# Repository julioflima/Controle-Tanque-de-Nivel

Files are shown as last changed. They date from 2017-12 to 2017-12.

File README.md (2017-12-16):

# Controle Tanque de Nível
## Projeto de Controle de Sistemas Dinâmicos - Engenharia Elétrica  - UFC

  Este projeto destina-se ao desenvolvimento de um controle de tanque de nível utilizando os conceitos de malha fechada. Como conrolador e sensor foram escolhidos respectivamente, o ATMEGA168-P e o HC-SR04.

  Os sistemas automáticos de níveis de água atualmente estão presentes em boa parte no cotidiano da vida humana, sejam em industrias ou mesmo nas casas, tendo em vista os conceitos de reutilização ou captação de água. Para controlar estes tipos de sistemas, geralmente utilizam-se de sensores de nível para acionamento da bomba e o controle pode ser feito a partir de um controlador PID ou por histerese, por exemplo. O relatório referente a este projeto se limitará à um controle realizado com base na histerese de sistemas de controle, nos quais os procedimentos serão apresentados mais adiante. A figura abaixo mostra um exemplo esquemático de um sistema hidráulico controlado pela bomba.

<p align="center">
  
</p>

  Para o sistema controlado, a histerese é implementada na forma dinâmica de um determinado atraso da saída em referência com a entrada, desde que esta seja lentamente variável. Este tipo de histerese é uma relação de dependência de taxas, ou seja, pode funcionar com sistemas que necessitem de armazenamento durável de memória. Esta técnica como controlador serve basicamente para filtragem de sinais a fim de que se obtenha uma saída mais lenta de acordo com a memória armazenada de um sinal mais recente. 
Em um sistema baseado em ações liga/desliga, este controle reduz a vida útil ou afeta os dispositivos conectados a este sistema. Por isso, a utilização da técnica de histerese torna-se interessante para sistemas do tipo, resultando, assim, em uma seleção de uma determinada faixa, por exemplo com temperatura, como mostra abaixo.

<p align="center">
  
</p>

  A IHM desenvolvida, teve como intuito a facilidade na hora de interagir na mudança do valor de referência e na visualização do nível atual do tanque independentemente da medição analógica, essa por meio de um duto transparente. Nela foi utilizada um display LCD 16x2, onde é possível a verificação dos valores. Dois botões para mudança no valor da referência. Dois barramentos, um destinado ao sensor ultrassônico, e o outro destinado a placa de driver. Uma saída seria, onde os valores de PWM, nível do tanque e valore de referência, são enviados ao computador para análise. Assim como o micro controlador ATMEGA328-P, responsável pelo controle e aquisição de dados. O esquemático e a placa discorrida nesta seção encontra-se nos anexos do relatório.
  
<p align="center">
  
</p>

  O sensor utilizado neste projeto é o sensor ultrassônico HC-SR04, utilizado para medir distâncias entre 2cm até 4m. Com o intuito de fixação na estrutura desenvolvia, o sensor foi encapsulado em um case como mostra a figura abaixo. O esquemático discorrido nesta seção, assim como mais detalhes encontra-se nos anexos do relatório.

<p align="center">
  
</p>

  O driver representa a parte de potência de um projeto, sendo este responsável pelo chaveamento de uma alta corrente, pois o controlador não suporta esse nível de potência, sendo assim indispensável. A placa de controle desenvolvida segue abaixo na figura abaixo.

<p align="center">
  
</p>

  Segue abaixo os gráficos relativos a dinâmica desse sistema, com o controle desenvolvido até então. Em verde o PWM, em vermelho a referência e em azul a elevação do nível da água.

<p align="center">
  
</p>

## FORK IT!

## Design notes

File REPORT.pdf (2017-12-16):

UFC - Campus Sobral

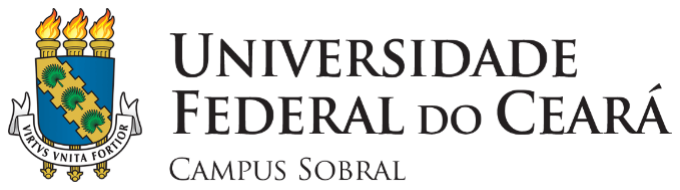
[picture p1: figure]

Controle de Sistemas Dinâmicos Professor Reuber Regis de Melo

Curso de Engenharia Elétrica

Laboratório de Sistemas de Controle

## Controle de Tanque de Nível

Alunos: Denisia Vasconcelos Mota

Julio Cesar Ferreira Lima

Renato Fonteles de Sousa

Prof.: Reuber Regis de Melo

Sobral, Dezembro de 2017

# SUMÁRIO

# INTRODUÇÃO

Os sistemas automáticos de níveis de água atualmente estão presentes em boa parte no cotidiano da vida humana, sejam em industrias ou mesmo nas casas, tendo em vista os conceitos de reutilização ou captação de água. Para controlar estes tipos de sistemas, geralmente utilizam-se de sensores de nível para acionamento da bomba e o controle pode ser feito a partir de um controlador PID ou por histerese, por exemplo. O relatório referente a este projeto se limitará à um controle realizado com base na histerese de sistemas de controle, nos quais os procedimentos serão apresentados mais adiante. A Figura 1.1 mostra um exemplo esquemático de um sistema hidráulico controlado pela bomba.

Figura 1.1 – Sistema hidráulico controlado.

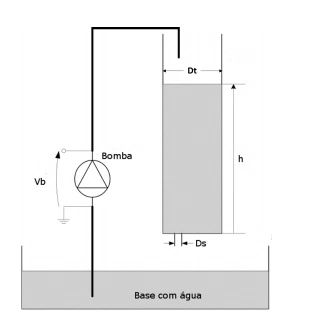
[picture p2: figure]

Fonte: Reuber Regis

Em um sistema deste tipo, é necessário saber alguns parâmetros para se atingir os níveis conforme se deseja no projeto implementado. Um destes parâmetros é o fluxo de entrada de líquido no tanque, que pode ser obtido com a equação (1) a seguir:
Fe = KbVb | (1)

Onde Kb é a constante de fluxo da bomba e Vb a tensão elétrica na mesma
Já a velocidade deste fluxo pode ser dada pela equação de Bernoulli, mostrada na equação (2) a seguir.
vs = √2gℎ | (2)

Onde g é a aceleração da gravidade e ℎ a altura de líquido no tanque.
A área e orifício do tanque podem calculados de acordo com o formato do tanque e do orifício. Para um tanque e orifício com formato cilíndrico, as áreas dos mesmo podem ser calculados conforme as equações (3) e (4) a seguir, respectivamente.

At =

πDt

2
4 | (3)

As =

πDs

2
4

(4)

Pode-se também com as equações já obtidas o fluxo de saída de líquido do tanque multiplicado a área do orifício pela velocidade do fluxo. Para o caso do formato cilíndrico de orifício, com a equação (5) obtém-se o fluxo de saída.
Fs = As√2gℎ | (5)

Assim, a taxa de fluxo do tanque pode ser obtida com a subtração entre o fluxo de entrada e o fluxo de entrada, resultando na equação (6) a seguir.
Ft = KbVb − As√2gℎ | (5)

Pode-se dizer que a taxa de fluxo do tanque é a derivada do volume em relação ao tempo e o volume pode ser calculado como a altura multiplicada pela área do tanque. Logo, de acordo com a equação (5) acima, após substituído o volume por Asℎ na derivada, pode-se isolar o ℎ. Encontra-se, assim, a equação (6) a seguir. dℎ dt =

KbVb − As√2gℎ At | (6)

Integra-se (6) para se encontrar uma equação para a altura. A equação (7) mostra a equação obtida:

ℎ(t) = ∫

KbVb − As√2gℎ
At

(7)

Para o equilíbrio do sistema, é necessário que o mesmo esteja no chamado ponto de operação. Pode-se assim linearizar a (7) a partir dos três primeiros termos da série de Fourier. Seja ℎ̂ = ℎ − ℎ0 e V̂b = Vb − Vb0 para pequenas variações de altura e tensão na bomba e o sistema atuante em um ponto de operação onde a taxa de fluxo seja igual a zero, a equação (8) mostra o resultado da equação linearizada para o projeto.
dℎ
dt = −

Asg√2
2At√gℎ0

ℎ̂ +

KbV̂b
At

(8)

Se na equação acima, for utilizado ℎ̂, como a derivada de ℎ0 é constante, pode-se escrever (8) como: dℎ̂
dt +

Asg√2
2At√gℎ0

=

KbV̂b
At

(8)

Aplicando a transformada de Laplace na equação (8), encontra-se a função transferência do sistema mostrada na equação (9).

G(s) =

Ĥ(s)
V̂b(s)

=

2Kb√gℎ0
2√gℎ0sAt + As√2g

(9)

Onde, da equação (9), pode-se generalizara função normalizada de malha aberta como na equação (10) a seguir.
G(s) =

Kdc
τs + 1

(10)

Onde Kdc (ganho DC) e τ (constante de tempo) são conforme (11) e (12), respectivamente:

Kdc =

Kb√gℎ0√2
Asg

(11)

τ =

√gℎ0sAt√2
Asg

(12)

Para o sistema controlado, a histerese é implementada na forma dinâmica de um determinado atraso da saída em referência com a entrada, desde que esta seja lentamente variável. Este tipo de histerese é uma relação de dependência de taxas, ou seja, pode funcionar com sistemas que necessitem de armazenamento durável de memória. Esta técnica como controlador serve basicamente para filtragem de sinais a fim de que se obtenha uma saída mais lenta de acordo com a memória armazenada de um sinal mais recente.
Em um sistema baseado em ações liga/desliga, este controle reduz a vida útil ou afeta os dispositivos conectados a este sistema. Por isso, a utilização da técnica de histerese torna-se interessante para sistemas do tipo, resultando, assim, em uma seleção de uma determinada faixa, por exemplo com temperatura, como mostra Figura 1.2.

Figura 1.2 – Exemplo de Histerese para temperatura.

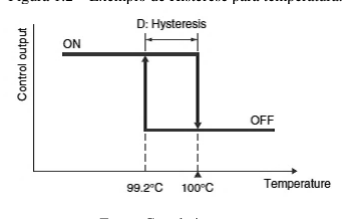
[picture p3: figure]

Fonte: Google imagens,

Onde na figura 02, duty cycle igual a 0,8 ºC para o valor de histerese 0,2%, a saída do sistema é desligada em 100 ºC e novamente ligada caso atinja a temperatura de 99.2 ºC.

# DESENVOLVIMENTO

## 1. Tanque

Para a construção do sistema físico foi feito uso de tubulações em PVC a fim de se obter caminho e encanamento para o fluxo de água, como também base e estrutura do mesmo material para o próprio sistema. Além disso, fez-se necessária na montagem a aplicação da bomba d’água do sistema ao lado inferior do tanque de reservatório, com intuito de garantir sempre a realimentação de água dentro das engrenagens da bomba. O resultado do sistema é mostrado abaixo pela Figura 2.1.

Figura 2.1 e 2.2 – (b) Sistema físico; (a) Posição da bomba d’água.

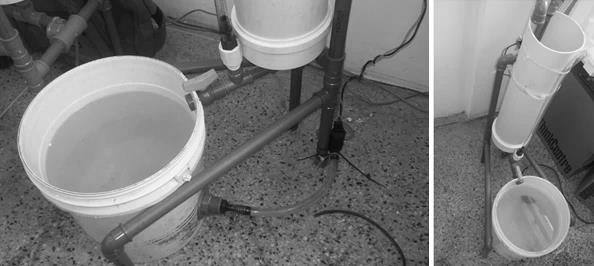
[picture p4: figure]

(a) (b)
Fonte: Próprio autor.

Como ilustra a Figura 2.2, para o tanque com altura a ser controlada, a equipe o construiu no sistema com tubulação de 150mm de diâmetro, uma altura máxima de 80 cm. O Reservatório trata-se de um balde com capacidade até 25 Litros, e para tubulação de fluxo e a estrutura de sustentação de 4 apoios, a matéria prima foi materiais de encanamento de 20 e 25 mm respectivamente de diâmetro. Assim, para o equacionamento, o tanque terá uma área de 56,25 cm².
Da equação 01, para o sistema utilizado em questão faz-se necessário saber as características físicas da bomba d’água utilizada. O grupo optou por utilizar um motor de corrente contínua utilizado em para-brisas de automóveis, com sua alimentação sendo 12V e máximos de corrente de aproximadamente 4,5 A. A Figura 2.3 a seguir mostra o modelo da bomba utilizada na implementação do projeto

Figura 2.3 – Bomba d’água TSN 12V.

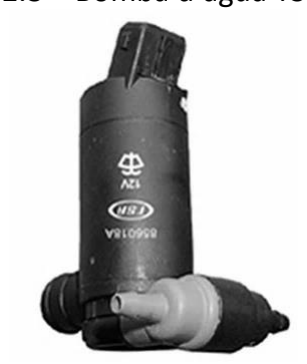
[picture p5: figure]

Fonte: Google Imagens.

Com isso, para o sistema utilizado, foi decidido utilizar como sinal de comando para a bomba um sinal PWM (Pulse Width Modulation) que se trata de um sinal periódico com ciclo de trabalho “d” variável, pois neste caminho, garantia-se valores de tensão os quais a bomba foi projetada, sempre em 0 ou 12 volts, diminuindo erros e não linearidades providas pela bomba. Dessa forma, a equação 01 terá uma relação periódica, onde deve ser utilizado a tensão média, calculada por:

Fe = Kb × Vbmédio

(13)

Ou seja, o cálculo dos valores médios de tensão na bomba Vbmédio dar-se pela seguinte forma:

Vbmédio =

1
T

∫ Vb

(t) × dt = ∫ 12 × dt

T∗d

0

T

0

+ ∫ 0 × dt

T

T∗d

= 12 × d | (14)

Portanto, substituindo a equação acima em 13, temos:

Fe = Kb × (d × 12)

(15)

Logo, para encontrar a constante da bomba, faz-se necessária o uso também de sinal PWM, o qual terá relação entre o fluxo dado pela equação anterior.

Com isso, de forma empírica, a equipe obteve no experimento medições de variação de altura da coluna d’água do sistema e qual o tempo levou esta variação de volume para determinado valor de ciclo de trabalho (d). Com a utilização de um micro controlador, junto a um circuito de chaveamento com MOSFET IRFZ648N, para experimento com a finalidade de se obter a constante da bomba, foi montado um circuito driver para a bomba d´água de acordo com o esquemático da Figura 2.5 a seguir:
Em seguida, com um programa simples dentro do micro controlador, de forma a guardar uma variável do tipo float em linguagem C/C++, o código simples é apenas um chaveamento com sinal alto no instante de tempo do ciclo de trabalho, e o desligamento no resto do período. Dessa forma, variando o valor da variável de ciclo de trabalho d, tem-se os resultados obtidos das medições feitas na tabela abaixo:

Tabela 2.1 – Variáveis para cálculo da constante da bomba Kb.
Ciclo de Trabalho | Δ Altura(m) | Δ Tempo(s) | Δ Volume(cm³) | Fluxo (cm³/s) | Kb
0,60 | 0,10 | 41,96 | 1767,14550 | 42,1150024 | 5,8493
0,70 | 0,10 | 58,27 | 1767,14550 | 30,3268492 | 3,6103
0,75 | 0,20 | 68,57 | 3534,29100 | 51,5428176 | 5,7270
0,80 | 0,06 | 19,61 | 1060,28730 | 54,0687047 | 5,6322
0,85 | 0,20 | 65,46 | 3534,29100 | 53,9916132 | 5,2933
0,90 | 0,10 | 31,90 | 1767,14550 | 55,3964107 | 5,1293
1,00 | 0,10 | 27,58 | 1767,14550 | 64,0734409 | 5,3395

Para os cálculos da tabela, com um cronômetro foi medido no sistema a variação da altura e qual o tempo em que o sistema levou para atingir àquela altura. Como os valores de área do cilindro de 75mm de raio são conhecidos, a variação do volume pode ser obtida. Por fim, o cálculo do fluxo é simplesmente a razão entre a variação do volume com a variação do tempo, onde com a equação 15, foi feita a coluna da tabela 01 para cálculo de Kb com a seguinte equação:

Kb(d) =

Fb
d × 12 =

∆Volume
∆tempo
d × 12

16

Fazendo um gráfico de dispersão, é possível notar os diferentes modos de comportamento da bomba, como mostra a Figura 2.4;

Figura 2.4 - Gráfico de dispersão para eixo x ciclo de trabalho e eixo y constante Kb.

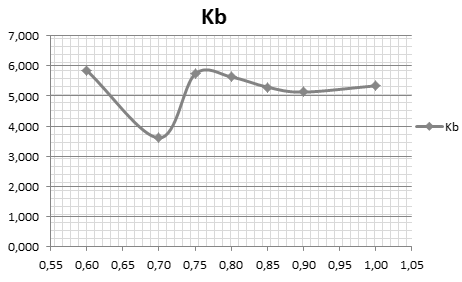
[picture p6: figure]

Fonte: Próprio autor.

Do gráfico, é notório a o erro relacionada a medição em “d” igual a 0,7, o que define um erro no momento da medição por fatores de problemas com a bomba, limitação de corrente da fonte ou a atuação da sobre carga que neste caso teve efeito maior por mudanças físicas da quantidade de água na bomba. Com isso, é válido fazer o cálculo final na constante Kb ignorando esses tipos de extremos encontrados.
Então, para o cálculo da constante Kb, pode-se adotar um dos valores encontrados, ou fazer um levantamento em cima das diferentes medições, calculando uma média aritmética da constante, que resultará em:

Kb =

5,849 + 5,727 + 5,632 + 5,293 + 5,129 + 5,329 6

= 5,945 | 17

Ainda no sistema físico, a equipe utilizou de uma chave reguladora de fluxo a fim de se ter controle quanto a vazão do fluxo de saída, permitindo assim ajustá-lo de acordo com a dinâmica do resto do sistema. Contudo, para o equacionamento faz-se necessária a área da secção transversal onde o fluxo cai no reservatório, algo quase impossível de se obter com equipamentos de medições ao tentar medir na chave reguladora de fluxo. Partindo da equação 5, sabemos que a área será:

As =

Fs
√2 × g × ℎ

=

1
√2 × g × ℎ

×

∆volume
∆tempo | 16

Então, a equação acima mostra que, com um valor constante de uma coluna d’água, calculando uma variação de volume e o tempo gasto, é possível estimar a área da secção transversal da vazão. Dessa forma, o grupo fez de forma empírica um experimento com intuito de calcular a área AD, mantendo uma altura h de 40cm. Com gravidade sendo 982 cm/s², temos a tabela feita para 5 medições da área, e uma estimativa média sendo: Tabela 2.2 – Estimativa da área da secção transversal do fluxo de saída:
Tempo(s) | Δ Volume (cm³) | Fluxo (cm³/s) | Área (cm²)
17,03 | 500,00 | 29,3599530 | 0,1048
16,21 | 490,00 | 30,2282542 | 0,1078
15,86 | 470,00 | 29,6343001 | 0,1057
15,80 | 450,00 | 28,4810127 | 0,1016
18,13 | 538,96 | 29,7275234 | 0,1061
Área Média | | | 0,1052

Portanto, os experimentos mostraram que o sistema tem constante da bomba KB igual a 5,945 e a área da secção transversal da tubulação de saída foi de 10,52 mm².

## 2. IHM (Interface Homem Máquina)

A IHM desenvolvida, teve como intuito a facilidade na hora de interagir na mudança do valor de referência e na visualização do nível atual do tanque independentemente da medição analógica, essa por meio de um duto transparente. Nela foi utilizada um display LCD 16x2, onde é possível a verificação dos valores. Dois botões para mudança no valor da referência. Dois barramentos, um destinado ao sensor ultrassônico, e o outro destinado a placa de driver. Uma saída seria, onde os valores de PWM, nível do tanque e valore de referência, são enviados ao computador para análise. Assim como o micro controlador ATMEGA168-P, responsável pelo controle e aquisição de dados. O esquemático e a placa discorrida nesta seção encontra-se nos anexos deste relatório.

Figura 2.5 – Placa desenvolvida para IHM.

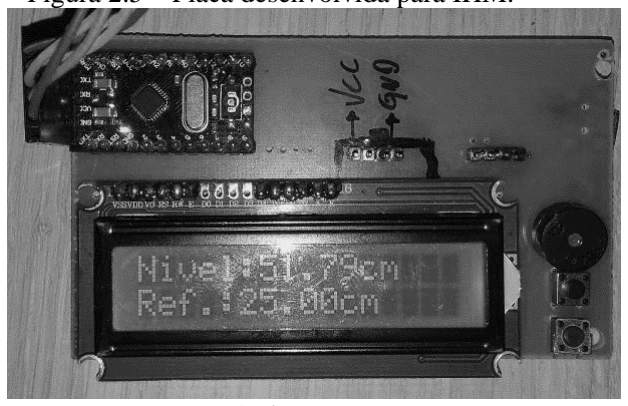
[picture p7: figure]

Fonte: Próprio autor.

Além da placa desenvolvida para a IHM, ainda há a possibilidade de conexão a um computador e assim fazer a análise dos dados. No entanto esse não é a principal vantagem desta conexão com a serial, e sim a possível plotagem dos gráficos e análise da dinâmica do sistema. Este é um dos grandes diferenciais deste projeto.

## 3. Sensor

O sensor utilizado neste projeto é o sensor ultrassônico HC-SR04, utilizado para medir distâncias entre 2cm até 4m. Com o intuito de fixação na estrutura desenvolvia, o sensor foi encapsulado em um case como mostra a Figura 2.6 abaixo.

Figura 2.6 – Sensor ultrassônico envolto em um case.

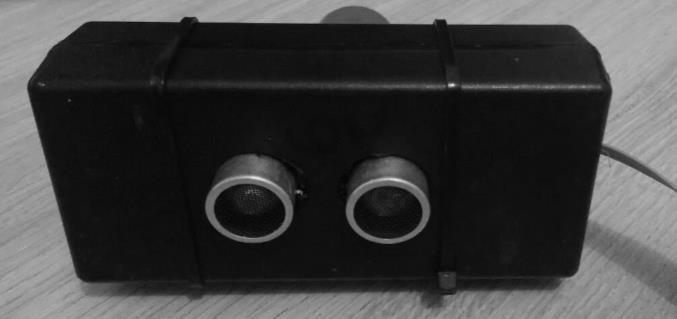
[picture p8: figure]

Fonte: Próprio autor.

O princípio de funcionamento deste sensor é baseado na velocidade do som no ar que é constate e de valor igual a 346,3m/s² se medido a CNTP. Por se tratar de uma grandeza constante, quando o sensor envia um pulso de sinal sonoro ele se propagará na velocidade do som, percorrerá o caminho, baterá no sólido, se encontrar um, a uma distância de até 4m e retornará o ECHO. Assim o micro controlador após o envio do sinal dispara um contador que só irá parar quando o ECHO for retornado, o valor deste contador multiplicado pela constante de velocidade do som no ar irá proporcionar o valor da distância percorrida, que deverá ser dividida por dois, pois esta representa a distância de ida e retorno do sinal de som, pois como o caminho percorrido é o mesmo, ambas são iguais. A Figura 2.7 abaixo ilustra o processo elencado acima. Já a Figura 2.8 ilustra o processo da variação do sinal elétrico que acontece nas portas digitais do micro controlador.

Figura 2.7 – Processo de medição de distância com sensor ultrassônico.

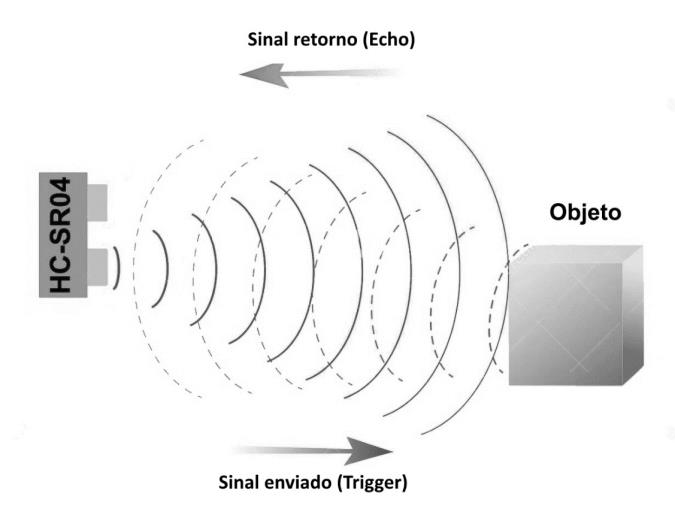
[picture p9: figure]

Fonte: Blog FilipeFlop.

Figura 2.8 – Processo elétrico nas I/Os do micro controlador.

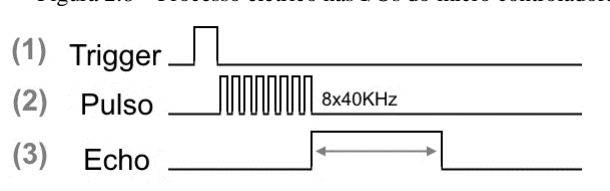
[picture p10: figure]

Fonte: Blog FilipeFlop.

## 4. Driver

O driver representa a parte de potência de um projeto, sendo este responsável pelo chaveamento de uma alta corrente, pois o controlador não suporta esse nível de potência, sendo assim indispensável. A placa de controle desenvolvida segue abaixo na Figura 2.9.

Figura 2.9 – Placa de circuito do driver.

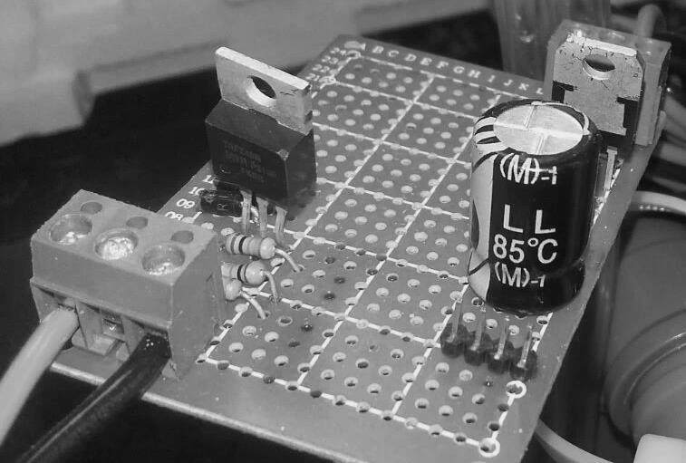
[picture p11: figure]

Fonte: Próprio autor.

A placa consiste em um borne para alimentação em 12V CC, e outro para a conexão com a bomba d’água, motor CC, neste caso. O pino de 12V parte direto para um dos terminais do motor, e a saída do motor será conectado no dreno de um MOSFET. Em antiparalelo com o motor será ligado um diodo ultra fast, na função de diodo de roda livre, para que possa fechar a malha e dissipar a corrente armazenada nos enrolamentos do motor, no momento em que ele for desligado, evitando o centelhamento, a propagação de ruído e possíveis problemas relacionados a chaves eletrônicas. Foi escolhido um diodo ultra fast, por conta do seu tempo de recuperação ser elevado, logo ele atuará de maneira rápida conduzindo a corrente, assim que o motor for desligado, ou passar por um ciclo onde a chave eletrônica o desliga. O MOSFET foi escolhido, por conta da sua baixíssima resistência de dreno source e comportando-se quase como uma chave perfeita e evitando, o aquecimento deste, evitando a necessidade de colocação de um dissipador de calor. Na gate do MOSFET foi colocado um resistor de pull-down, assim evita que na presença de um ruído esterno ou instabilidade do sistema o MOSFET conduza. Novamente entre o gate e o borne de conexão com o micro controlador foi colocado um resistor para limitação da corrente oriunda do micro controlador, este resistor não é necessariamente necessário, é apenas uma questão de proteção para o micro controlador em caso de mal funcionamento da chave. O circuito foi pensado de modo a funcionar de maneira desacoplada de duas fontes de alimentação, bastando assim apenas a alimentação da placa do driver. Neste intuito foi inserido um CI de regulação de tensão LM7805, que tem a função de reduzir e mantar na saída 5V CC, com valores de entrada que podem variar de 35V a 5V. Além do regulador foram adicionados uns capacitores para filtragem de frequências altas, assim como controle do ripple oriundo da fonte. A saída deste regulador, juntamente com o ground e pino de entrada para o resistor do gate, foram ligados em um barramento de com 4 pinos, poderiam ser utilizados apenas 3 pinos, porém por uma preferência em manter o padrão oriundo do circuito de IHM, foi optado por manter os quatro e deixando assim um pino não conectado a nada. O esquemático discorrido nesta seção encontra-se nos anexos deste relatório.

## 5. Controle

O controle utilizado neste projeto, foi o PWM (Pulse Width Modutation), que compreende na variação da largura de pulso de uma onda quadrada de frequência fixa, desse modo é variada a energia na saída. No sistema de um motor CC de rotação relativamente baixa o controle com variação de energia, por PWM, em uma frequência de 500Hz é funciona relativamente bem, pois trata-se de uma relação de frequência de controle e frequência de atuação alto, isto é a frequência do controle é muito mais alta que a frequência que o motor trabalha. A variação da energia, ocorre com a variação do duty cicle, que compreende na porcentagem em que o pulso permanece em nível alto, a cada ciclo. Assim a variação do duty cicle provocará a variação da energia variando a tensão média aplicada nos terminais do motor.

Figura 2.10 – Variação de tensão média por PWM.

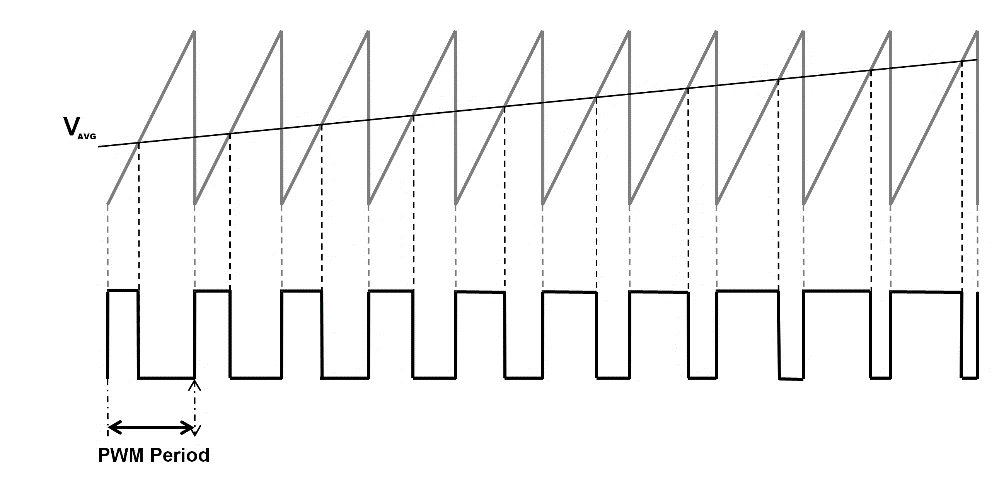
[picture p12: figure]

Fonte: Google imagens, editado pelo autor.

### 1. Definição de Constantes

Primeiramente foram definidas as constantes relativas aos erros provocados pelo tanque nível em relação ao sensor. Após a fixação do sensor em seu devido local de operação, com o tanque vazio foi anotado o valor mostrado. Este valor corresponde a distância total do sensor ao fundo do nível.
Após o processo citado no próximo tópico ainda se observou um erro relativo ao fundo real do tanque em relação a régua de medição, pois o nível indicava um número inferior ao mostrado pelo nível analógico, isso se dá pelas relações não lineares, por conta de conexões da estrutura no fundo do tanque. A diferença que faltava para a que as duas medidas fossem iguais foi anotada.
A constante de histerese trata-se da distância em que o controlador irá preocupar-se com o controle, isto dentro da região de histerese o sistema estabiliza-se, não havendo mais incrementos ou decrementos pelo controlador. Então esta constante precisará ser definida de modo que o sistema não fique demasiado lento, como também não apresente muito ruído ao estabilizar-se. Esta constante foi obtida determinando inicialmente um valor que se acreditava ser um bom parâmetro, de forma intuitiva. A posteriori tal constante foi modificado, para observação se melhores resultados eram encontrados. Ao fim se percebeu que a determinação da constante ideal era a considerada inicialmente.
Precisa-se de um valor inicial para o valor de referência, como o tanque possui cerca de 50cm de comprimento, optou-se pelo valor médio.
Deste modo tais constantes elaboradas seguem abaixo, respectivamente na ordem que foram apresentadas:
- clvlwater: 47.59
- deltaSystem: 0.5
- waterlvl: 25
- offset_lvlwater: 4.2

### 2. Medição

A cada ciclo no main() do programa que acontece a cada 10ms, o micro controlador faz a leitura da distância. No entanto, como neste trabalho o intuito não é a medição da distância do sensor ao nível do tanque e sim do nível zero do tanque até o seu valor mais alto, se subtrai da variável clvlwater o valor de distância medido e por sua vez se soma o erro relativo a medição da distância pelo sensor até o fundo do tanque offset_lvlwater. Dessa forma o sinal resultante é de fato a leitura do nível do tanque em relação ao nível zero.

### 3. Atuação

A atuação, acontecerá de maneira incremental, se a distância capturada estiver acima do nível de referência, será subtraído o duty cicle do PWM e verificado de novo se atendeu a referência, fechando assim a malha para o primeiro caso. O segundo caso é análogo ao primeiro, onde ele irá incrementar o duty cicle do PWM, e então verificar sua distância do ponto de referência. O circuito estabilizará se o nível estiver sempre no nível de referência com uma variação compreendida dentro do intervalo de histerese, ou situado em algum dos limites do duty cicle do PWM, onde não fosse possível o incremento ou o decremento deste, por conta do sistema ser não linear e haver os limites 100% e 0%. Segue na Figura 2.11 abaixo o gráfico gerado em tempo real de acordo com os dados enviados pela porta serial do micro controlador. Em verde o PWM, em vermelho a referência e em azul a elevação do nível da água.

Figura 2.11 – Gráfico da dinâmica do sistema controlado em operação.

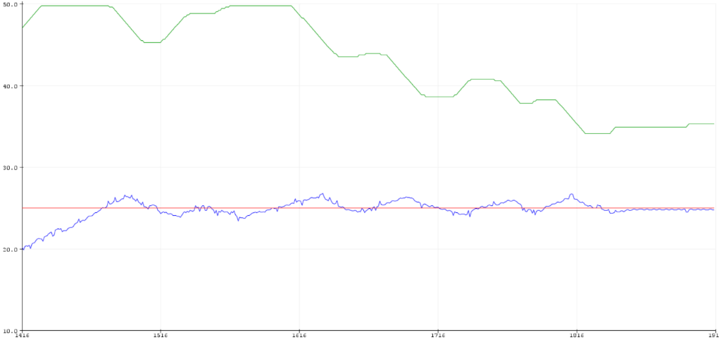
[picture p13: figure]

Fonte: Google imagens, editado pelo autor.

# REPOSITÓRIO PÚBLICO

Este trabalho não tem o intuito de ser descontinuado ao fim desta disciplina, de modo que ele seja

perpetuado e possa contribuir para a formação dos integrantes, juntamente com a formação de alguém que

deseja um fim próximo ao que se destinou aqui. Será postado em uma plataforma aberta, tanto os modelos de

esquemático da placa que envolve o micro controlador e o sensor ultrassônico, quanto a placa de driver de

potência.

Será adicionada uma licença pública de livre modificação e uso de tudo desenvolvido dentro deste

projeto, chamada licença MIT.

O link para acesso do repositório, segue abaixo:

- https://github.com/juloko/Controle-Tanque-de-Nivel

A seções dentro do repositório são divididas abaixo:

- code: Diretório destinado a colocação do código rodado dentro do micro controlador. O ambiente

de desenvolvimento utilizado foi a IDE Arduino.

- libraries: Diretório destinado a colocação das bibliotecas utilizadas dentro do código do micro

controlador. As bibliotecas foram produzidas para a linguagem C, compatível com o compilador

Arduino.

- sensor: Diretório destinado a colocação das do esquemático e placa do sensor, concebido aqui

como a união do circuito do micro controlador com o barramento do sensor. Tais arquivos são

destinados a produção da placa de circuito impresso. Os arquivos encontram-se no formado do

software KICAD.

- driver: Diretório destinado a colocação das do esquemático do circuito de acionamento da bomba,

conhecido como driver, destinada a produção do circuito. Os arquivos encontram-se no formado

do software KICAD.

- REPORT: Arquivo com este relatório.
- README: Arquivo com explanação sobre aspectos gerais deste relatório.

# CONCLUSÃO

Idealmente o controle elaborado nesse projeto, não deveria ter procedido da maneira que foi. O conjunto

micro controlador e sensor, deveria apenas ter funcionado unicamente como um sensor. No entanto a

problemática de não haver um conversor digital analógico, D/A, impossibilitou o prosseguimento do projeto

sem que houvesse a implementação do controlador via código, já que não se conseguiria uma razão de

proporção na entrada do amplificador operacional que fosse possível a comparação de erro.

No entanto, o projeto mostrou-se satisfatório, uma vez que ele consegue atingir o estado permanente. No

entanto não foi possível a estabilização da bomba, pois a resposta do controlador é demasiado lenta em relação

a dinâmica do sistema. Nos gráficos gerados no experimento, foi possível a verificação senoidal na variação

do erro de estado permanente, em torno da referência de nível. Também foi notada uma semelhante relação em

relação ao acionamento da bomba, uma vez que em determinado período de tempo, constante dado pela

constante de tempo característica do sistema, ela comportava-se de maneira senoidal variando entre os limiares

onde havia cem por centro do duty cicle do micro controlador e zero por cento.

# BIBLIOGRAFIA

[1] OGATA, Katsuhiko. Engenharia de Controle Moderno. 4ª edição. Editora Prentice Hall.
[2] REGIS DE MELO, Reuber. Modelagem da dinâmica física do tanque de nível. Laboratório de Controle

de Sistemas Dinâmicos.

[3] POULSEN, Soren. ANDERSEN, Michael A. E. . Hysteresis Controller with constant switching

frequency. Technical University of Denmark. Disponível em:

<http://www.skory.gylcomp.hu/alkatresz/pwm_amp(fixfreq_onrezgo).pdf>. Acesso em Dezembro de

2017.

[4] WIKIPEDIA. Hysteresis. Disponível em: <https://en.wikipedia.org/wiki/Hysteresis>. Acesso em

Dezembro de 2017.

[5] OMRON. Temperature Controller: Hysteresis. Disponível em: <http://www.omron-

ap.com/service_support/FAQ/FAQ00549/index.asp>. Acesso em Dezembro de 2017.

# ANEXOS

// Carrega as bibliotecas, sensor ultrassonico e LCD. #include <Ultrasonic.h>
#include <LiquidCrystal.h>

// Declara a variável de referência do nível da água. float waterLvl = 25;

// Declara a variável que armazena a distância recebida. float distance = 0;

// Declara a variável de tempo para plotar os valores. float timerPrint = 0;

// Declara a variável do duty cicle do PWM.
float duty = 0;

// Declara a variável de tempo para o controlador. float timerControl = 0;

// Define as constantes do sistema.
#define timeSystem 10

#define timeControl 2*timeSystem #define timePrint 100*timeSystem #define clvlwater 47.59

#define offset_lvlwater 4.2

// Define a constantes histerese de distância. #define deltaSystem 0.50

// Declara e define os pinos utilizados pelo LCD.
// Inicializa a biblioteca do LCD, com os pinos que serão utilizados. const int constraste = 10, rs = 4, en = 5, d4 = 6, d5 = 7, d6 = 8, d7 = 9; LiquidCrystal lcd(rs, en, d4, d5, d6, d7);

// Declara e define os pinos para o trigger e echo.
#define pino_trigger 15

#define pino_echo 14

// Inicializa o sensor nos pinos definidos acima. Ultrasonic ultrasonic(pino_trigger, pino_echo);

// Declara e define o pino utilizado no PWM. #define pwm 11

// Define os pinos utilizados nos botões. #define btn_01 2
#define btn_02 3

void setup()
{
// Attach the Extern Interruptions. attachInterrupt(digitalPinToInterrupt(btn_01), upLvl, FALLING); attachInterrupt(digitalPinToInterrupt(btn_02), downLvl, FALLING);

// Muda o constraste do LCD.
analogWrite(constraste, 50);

// Iniciliza a Serial, com sua velocidade.. Serial.begin(9600);

// Seta os números o número linhas e colunas do LCD.

lcd.begin(16, 2);

// Escreva no LCD, Controle Analógico em inglês. ;) lcd.write("Analogic Control");

//Aplica delay de 1s.
delay(2000);
}

void loop()
{
// Recebe distância do nível da água.
distance = getDistance();

// Plota o nível referência do nível da água no LCD, a cada 1s. printLCD(distance);

// Plota o nível referência do nível da água na Serial. printSerial(distance);

// Controla.
pwmDistance((12 / 6) * 255); }

// Exibe informações no LCD, a cada 1s.
void printLCD(float distance) {
if ((millis() - timerPrint) >= timePrint) { timerPrint = millis();

lcd.clear();
lcd.setCursor(0, 0);
lcd.write("Nivel:");
lcd.print(distance);
lcd.print("cm");
lcd.setCursor(0, 1);
lcd.write("Ref.:");
lcd.print(waterLvl);
lcd.print("cm");
}
}

// Exibe informações na Serial.
void printSerial(float distance) { Serial.print("Nivel em cm: "); Serial.print(distance);
Serial.print(" | ");
Serial.print("Referencia em cm: "); Serial.print(waterLvl);
Serial.print(" | ");
Serial.print("Duty: ");
Serial.println((duty / 255) * 50);
}

// Plota no duty do PWM o valor do nível da água. void pwmDistance(float duty) { analogWrite(pwm, duty);
}

// Retorna a distancia do nivel da água. float getDistance() {
float cmMsec;
for (int i = 0; i<1; i++) {
// Lê as informacoes do sensor, em cm.

long microsec = ultrasonic.timing();
cmMsec += ultrasonic.convert(microsec, Ultrasonic::CM); delay(timeSystem);
}
return clvlwater - cmMsec / 1 + offset_lvlwater;
}

// Incrementa em 0.01 o nível de referência da água. void upLvl() {
while (!digitalRead(btn_01)) {
if (waterLvl<50) {
waterLvl += 0.01;
printLCD(distance);
delay(100);
}
}
}

// Decrementa em 0.01 o nível de referência da água. void downLvl() {
while (!digitalRead(btn_02)) {
if (waterLvl>0) {
waterLvl -= 0.01;
printLCD(distance);
delay(100);
}
}
}

void digitalControl(float distance, float waterLvl) {
// Controle de Histerese de Tempo.
// Apenas irá controlar quando o tempo de captura espaçar 200ms desde a última leitura if ((millis() - timerControl) >= timeControl) {
timerControl = millis();

// Controle de Histerese de Distâncias.
// Verifica se a diferença entre o nível e a referência é superiores a 0.5cm. if ((distance - waterLvl) > deltaSystem) {
pwmDistance(setDuty(duty - 1));
}
else if ((distance - waterLvl) < -deltaSystem) { pwmDistance(setDuty(duty + 1));
}
}
}

int setDuty(int _duty) {
if (_duty < 255 && _duty > 0) { duty = _duty;
}
return duty;
}

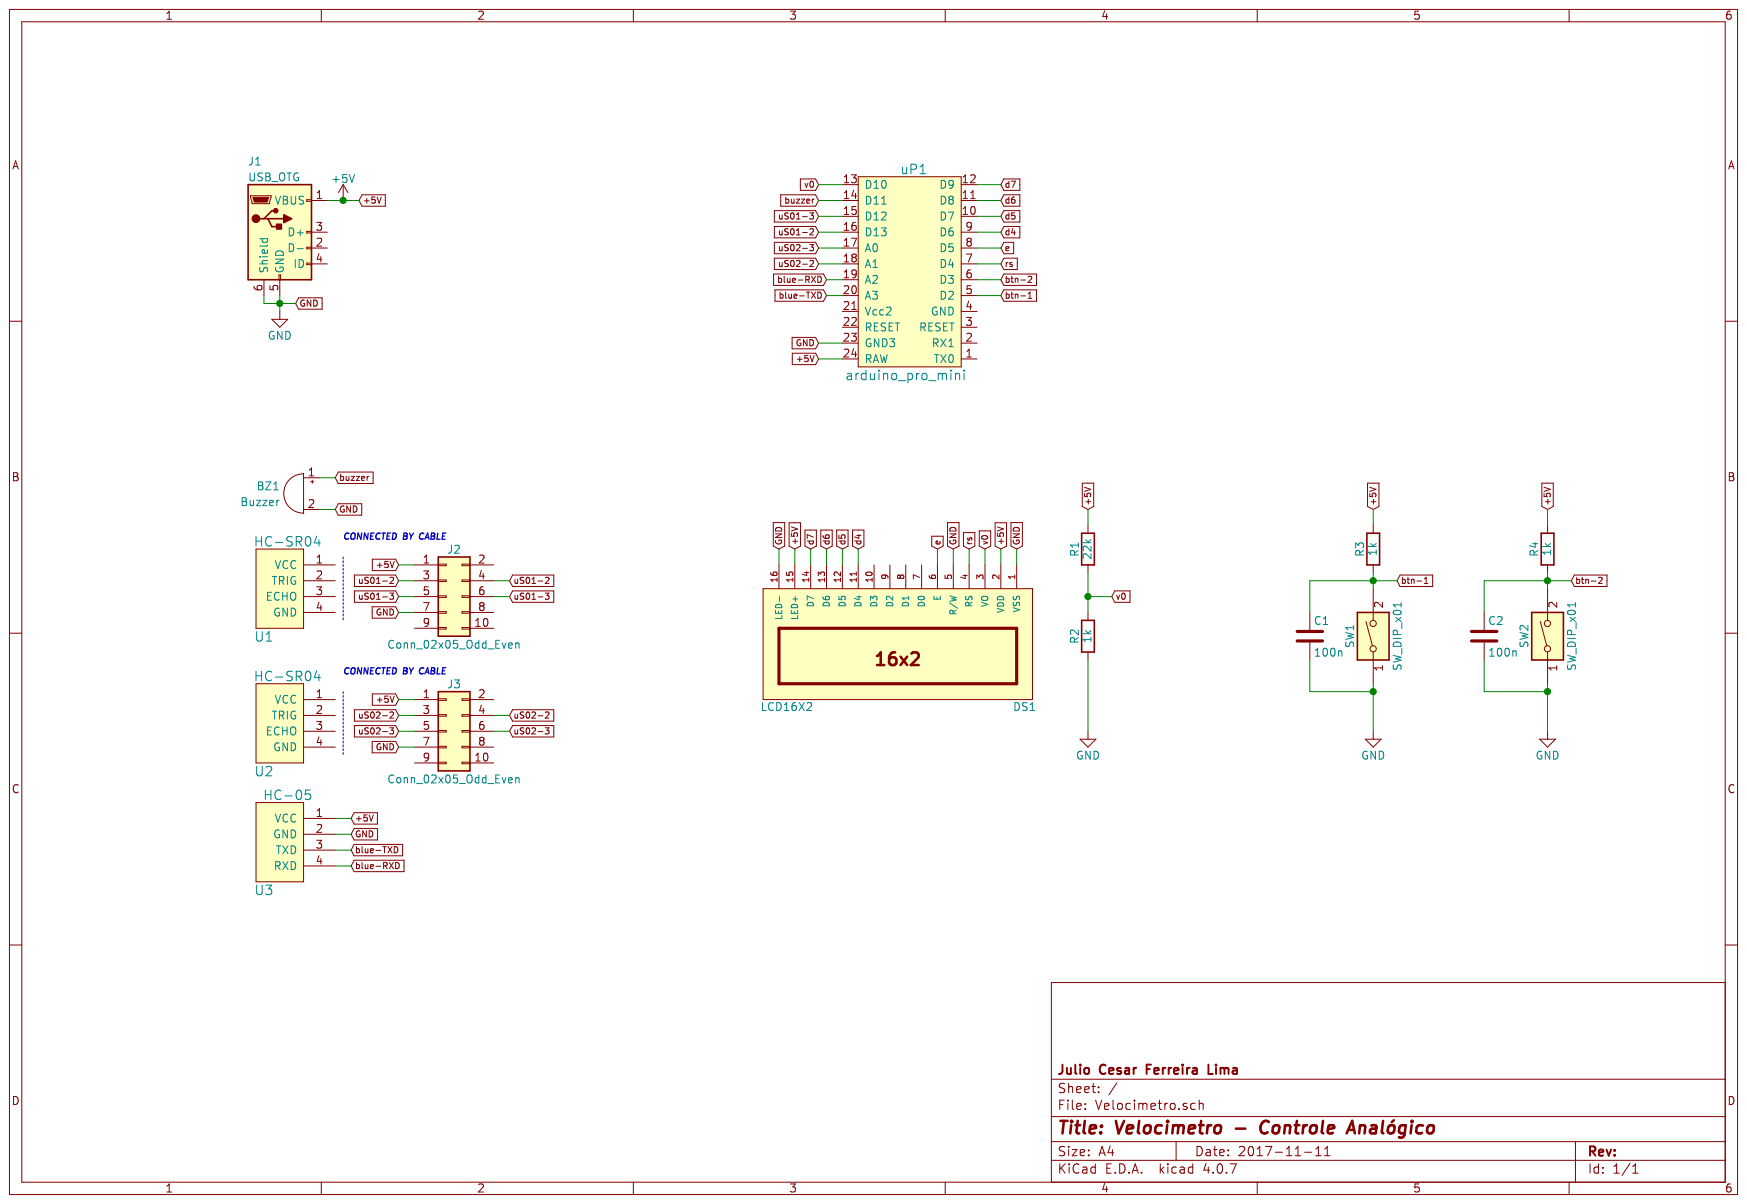
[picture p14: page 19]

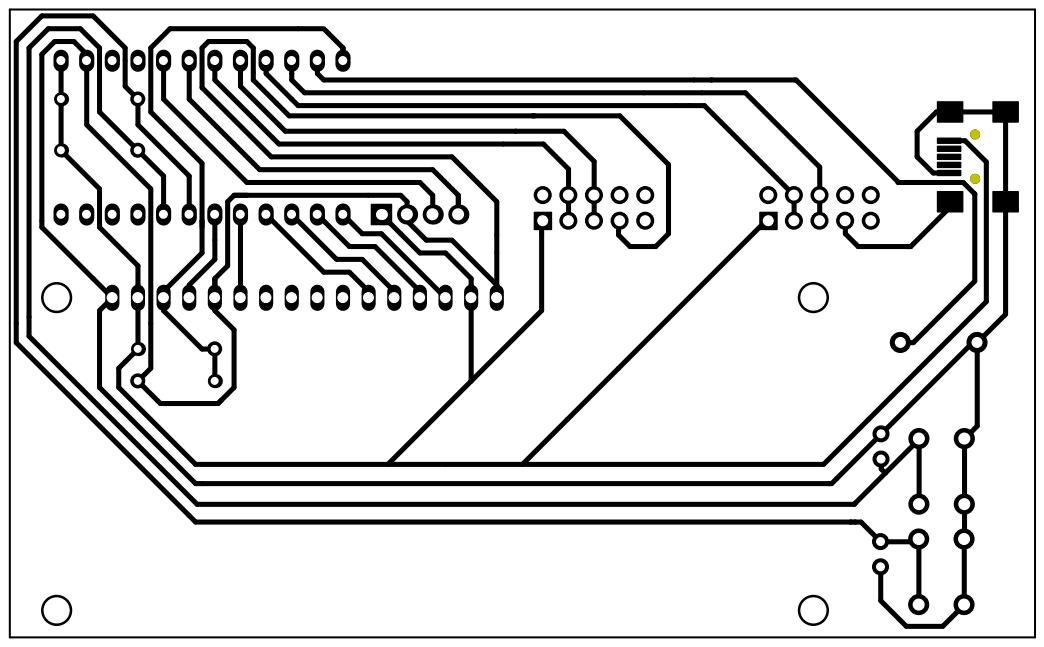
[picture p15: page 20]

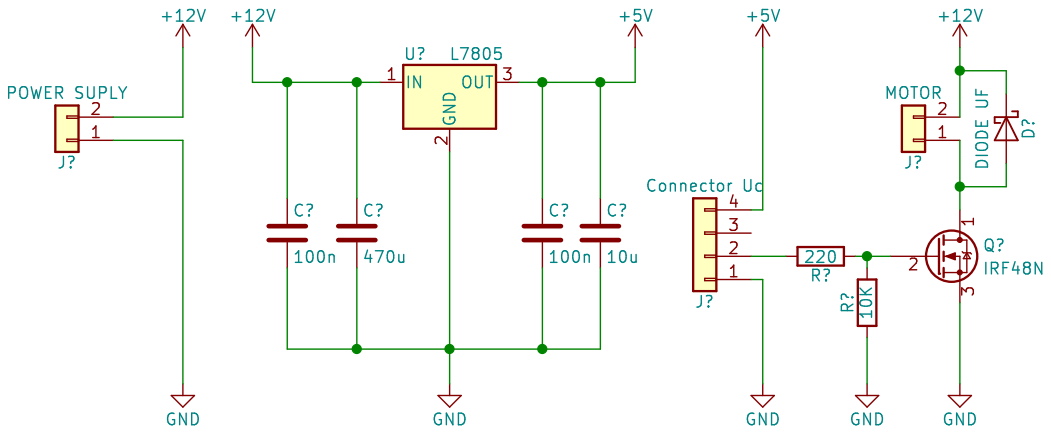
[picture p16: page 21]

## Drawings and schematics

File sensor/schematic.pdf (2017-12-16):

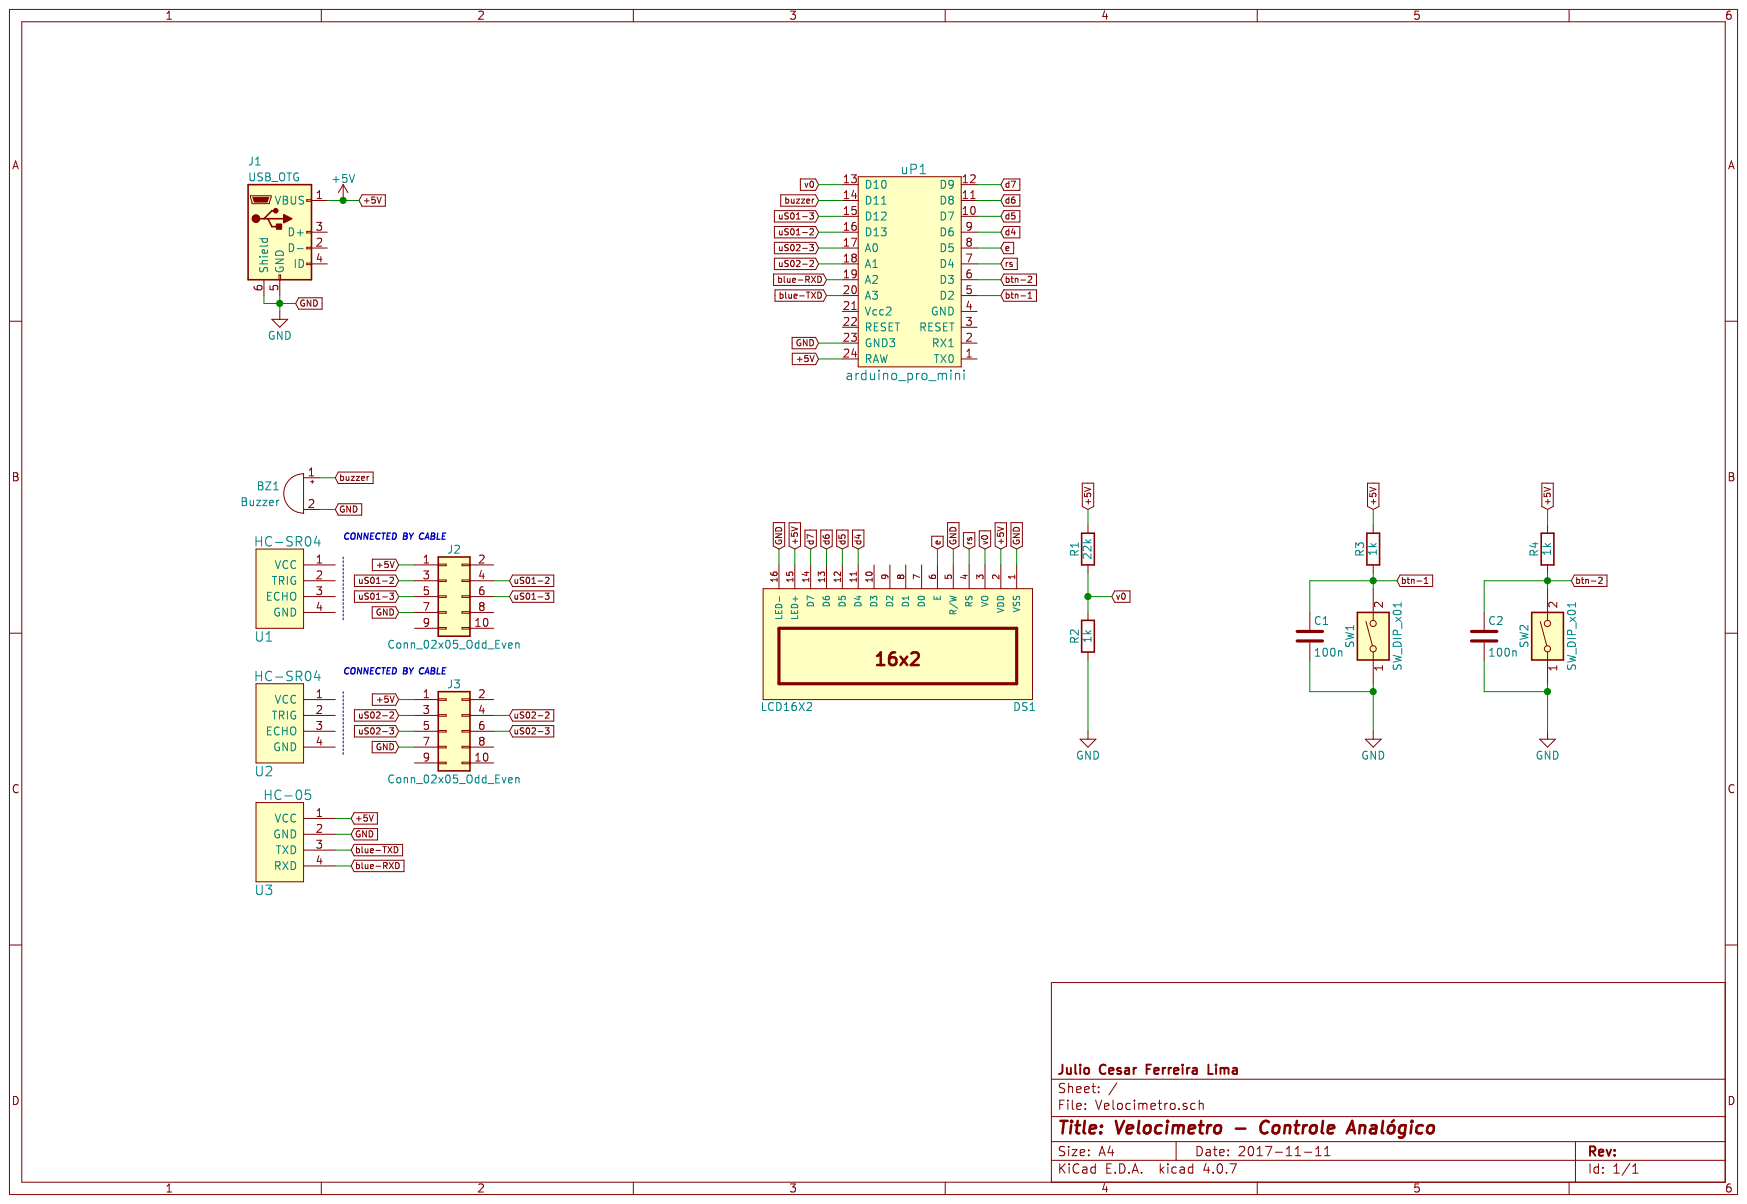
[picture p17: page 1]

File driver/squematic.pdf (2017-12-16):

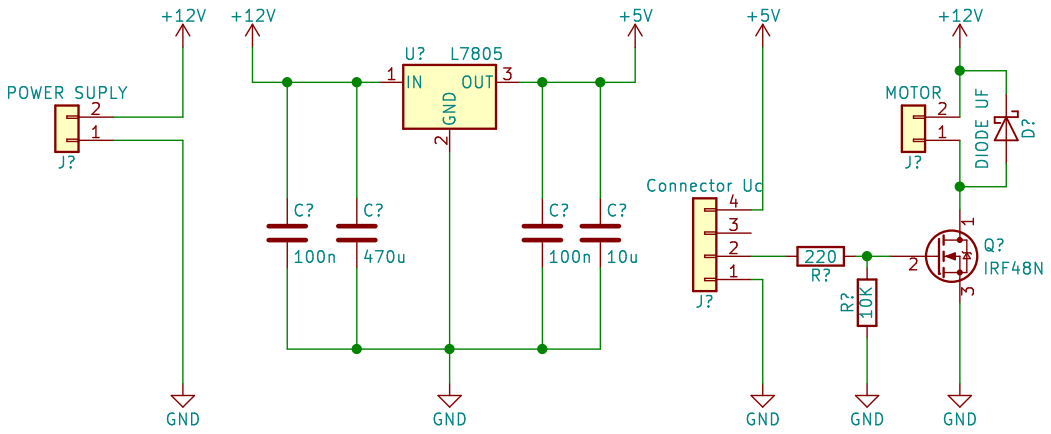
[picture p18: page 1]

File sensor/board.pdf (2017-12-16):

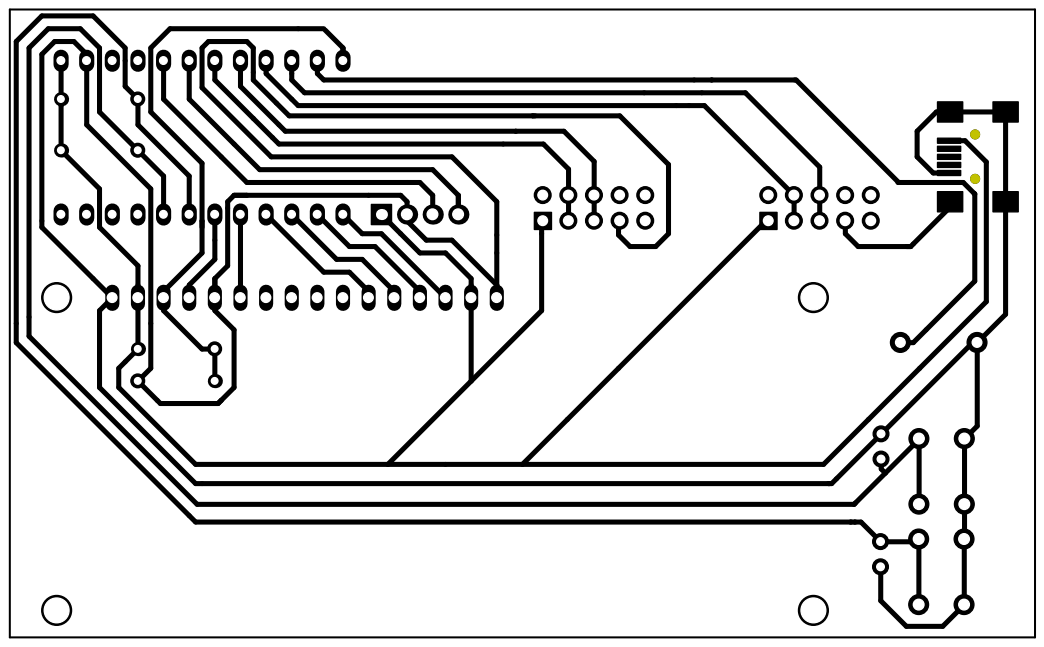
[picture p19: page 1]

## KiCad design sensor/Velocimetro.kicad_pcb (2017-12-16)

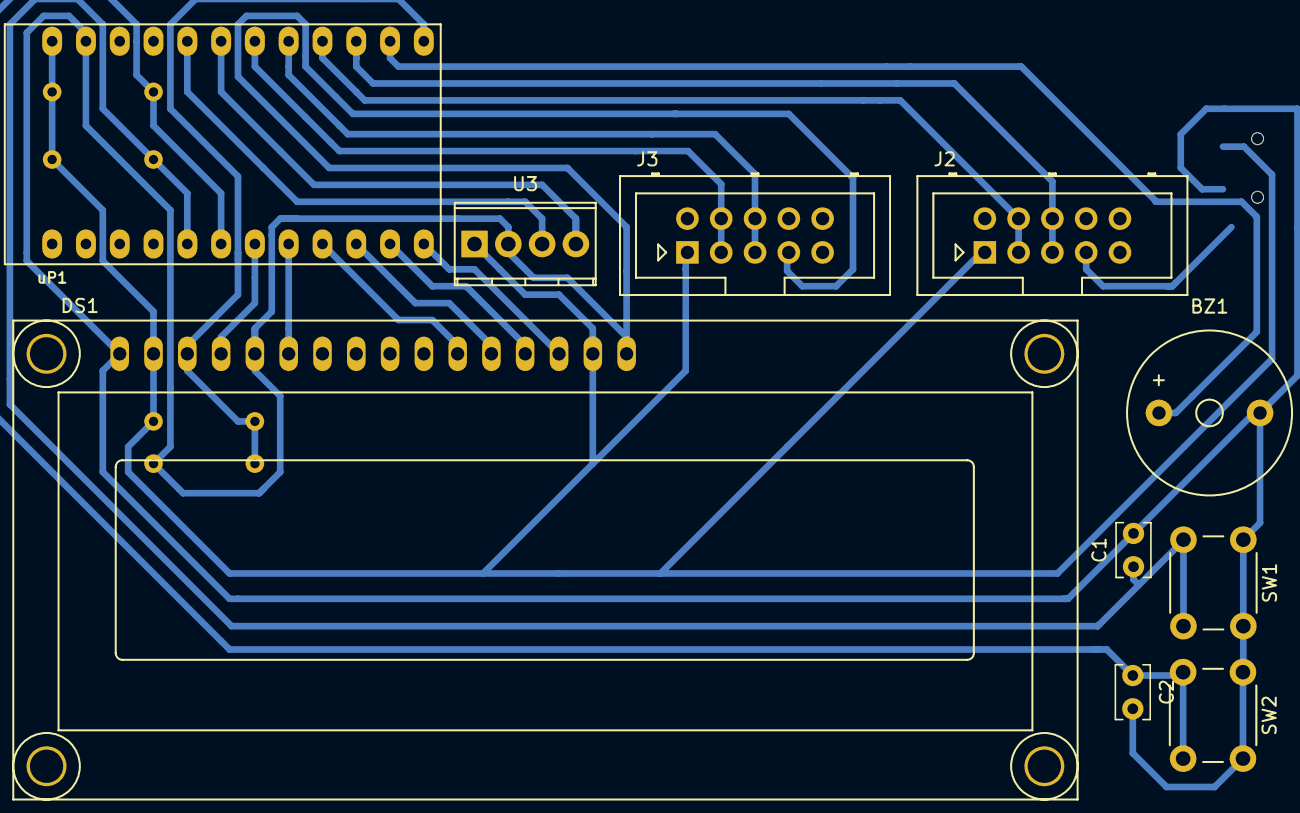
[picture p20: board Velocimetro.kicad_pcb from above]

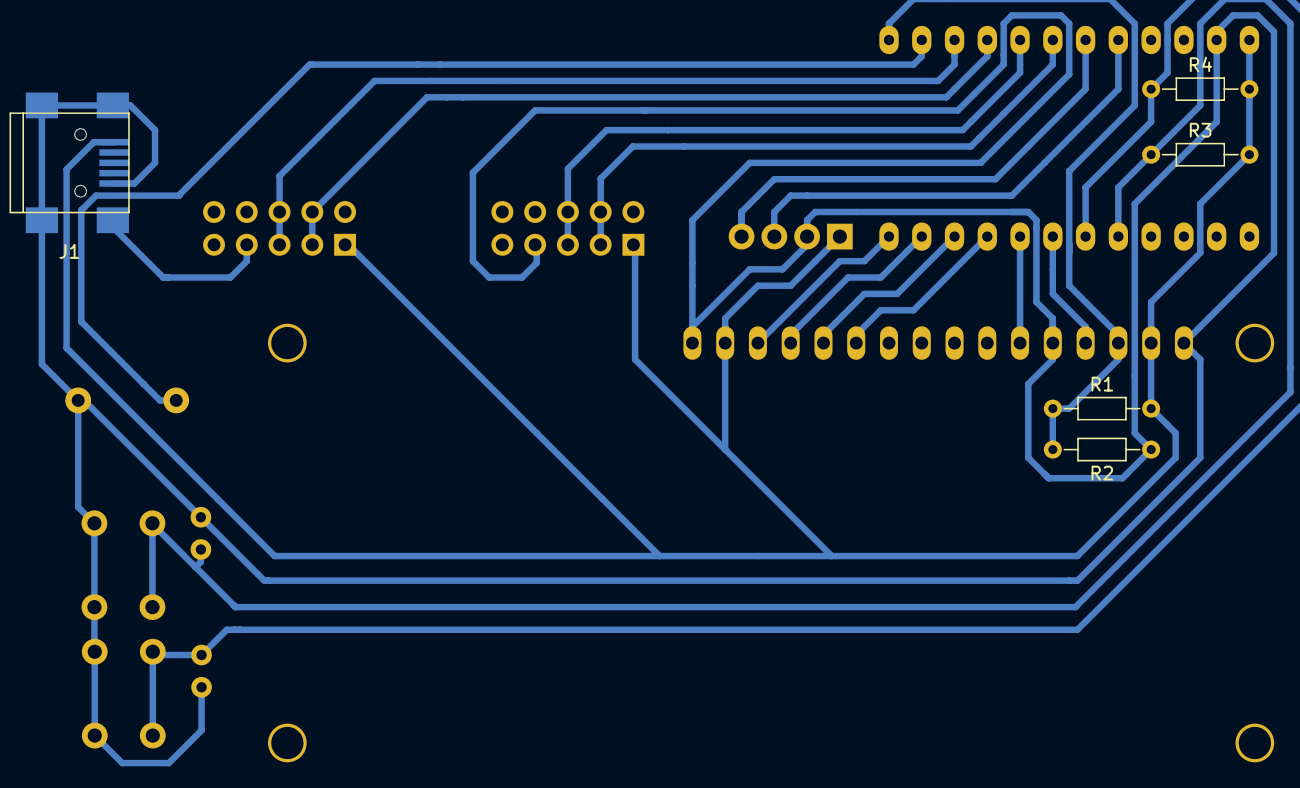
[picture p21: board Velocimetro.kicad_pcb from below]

Board: 2 copper layers, 15 parts (5 on the bottom side), 18 nets.

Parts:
BZ1: Buzzer; Buzzer_12x9.5RM7.6
C1, C2: 100n; C_Rect_L4.0mm_W2.5mm_P2.50mm
DS1: LCD16X2; WC1602A
J1: USB_OTG; USB_Mini-B
J2, J3: Conn_02x05_Odd_Even; Multicomp_MC9A12-1034_2x05x2.54mm_Straight
R1: 22k; R_Axial_DIN0204_L3.6mm_D1.6mm_P7.62mm_Horizontal
R2, R3, R4: 1k; R_Axial_DIN0204_L3.6mm_D1.6mm_P7.62mm_Horizontal
SW1, SW2: SW_DIP_x01; SW_PUSH_6mm
U3: HC-05; TerminalBlock_Phoenix_MPT-2.54mm_4pol
uP1: arduino_pro_mini; pro_mini

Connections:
+5V: DS1.2, DS1.15, J1.1, J2.1, J3.1, R1.2, R3.2, R4.2, U3.1, uP1.24
GND: BZ1.2, C1.2, C2.2, DS1.1, DS1.5, DS1.16, J1.5, J1.6, J2.7, J3.7, R2.1, SW1.1, SW2.1, U3.2, uP1.23
blue-RXD: U3.4, uP1.19
blue-TXD: U3.3, uP1.20
btn-1: C1.1, R3.1, SW1.2, uP1.5
btn-2: C2.1, R4.1, SW2.2, uP1.6
buzzer: BZ1.1, uP1.14
d4: DS1.11, uP1.9
d5: DS1.12, uP1.10
d6: DS1.13, uP1.11
d7: DS1.14, uP1.12
e: DS1.6, uP1.8
rs: DS1.4, uP1.7
uS01-2: J2.3, J2.4, uP1.16
uS01-3: J2.5, J2.6, uP1.15
uS02-2: J3.3, J3.4, uP1.18
uS02-3: J3.5, J3.6, uP1.17
v0: DS1.3, R1.1, R2.2, uP1.13
